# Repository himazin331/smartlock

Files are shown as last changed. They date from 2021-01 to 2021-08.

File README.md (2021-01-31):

# セキュアなスマートロックを作りたい

## 概要
**顔認証**(生体)とスマホの**MACアドレス認証**(所有)の二要素認証で解錠するスマートロックをつくる。
また、遠隔でも解錠/施錠できるようにWebアプリケーションを通じて制御できるようにする。

玄関ドアの外側に**TTGO T-camera**(人感センサー付カメラ)を取り付ける。モバイルバッテリーなどで供給する。(ドアの構造上及びコンセントがないため)

消費電力を抑えるために、施錠状態かつ人を感知したときにのみ認証を試みる。

スマホのMACアドレスは自宅WiFiに自動接続されたときにarpコマンドにより取得する。

## システム構成
システム構成図

 - **Webアプリケーション**
AAA.himazin331.comはCGI用FQDN。BBB.himazin331.comはラズパイ用FQDN(サブドメインは秘匿)
AAA.himazin331.comはSSL/TLS暗号化させMixed Content回避。BBB.himazin331.comはDDNSによって自宅のグローバルIPと紐付ける。

- **認証**
TTGO T-cameraはSTAモードで稼働させ自宅LANに接続させる。
UDP通信では、ラズパイがT-cameraに施錠状態であることを伝える、T-cameraがラズパイに人を感知したことを伝えることをする。
HTTP通信ではラズパイがT-cameraのカメラサーバーにリクエストし、カメラ画像を取得する。

BBB.himazin331.comをSSL/TLS暗号化させれば楽なのだが、私のネットワーク環境はIPv6 IPoE(IPv4 over IPv6)のため80, 443番ポートを開放できず、Let's EncryptのHTTP-01チャレンジができなかった。また、ラズパイ - Azure間をOpenVPNで通信の秘匿化を図ったが、なぜかWebページが表示されなくなってしまったので断念。

## シーケンス図

### Webアプリケーション
Webアプリケーション-シーケンス図

### 認証
認証 - シーケンス図

## 回路図
回路図

入力コンデンサ0.033μFとあるが、0.33μFが適切である。([datasheet](https://akizukidenshi.com/download/ds/st/l78.pdf)より)
しかし、手違いで0.033μFのコンデンサ使い実装してしまった。
一応、動作に影響はないが差し替える予定。

## 実体配線図
実体配線図

当初はGPIO 4番を使う予定だったが、実装中に短絡して不能になってしまったため、GPIO 14番に変更。

## 使用ハードウェア
- Azure VM (米国西部2 CentOS 7.8.2003 Standard B1s (1 vcpu 数、1 GiB メモリ))
- Raspberry Pi Zero WH
- MG996R ([datasheet](https://akizukidenshi.com/download/ds/towerpro/mg996r.pdf))
- 9V-2A ACアダプタ
- 三端子レギュレータ L7806CV ([datasheet](https://akizukidenshi.com/download/ds/st/l78.pdf))
- MOS-FET INK021ABS1-T112 ([datasheet](https://akizukidenshi.com/download/ds/isahaya/INK021ABS1_J.pdf))
- その他電子部品
- TTGO T-Camera ESP32 WROVER & PSRAM Camera Module ([商品リンク](https://www.amazon.co.jp/gp/product/B07PPR8Z2S/))
- 適当なモバイルバッテリー
- 3Dプリンタ (ガワ造形)

## 使用言語
- Python
- C/C++
- HTML/CSS
- Javascript

## 使用ライブラリ
- Apache
- Ajax
- Tensorflow, Tensorflow Lite
- pigpio
- OpenCV
- [T-camera Demo Program](https://github.com/lewisxhe/esp32-camera-series
)

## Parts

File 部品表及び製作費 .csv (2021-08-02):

名称 | 数量 | 購入場所 | 価格(税込) | 備考
ANYCUBIC PLA樹脂 1.75mm フィラメント シルバー | 146 g | Amazon | ¥423 | 1kg ¥2,899 サムターンマウンタ: 20g サーボモータ固定マウンタ: 44g 制御基板ステージ: 31g 制御基板ステージ蓋: 13g T-cameraマウント: 14g ケーブルフック: 6g x 4
Raspberry Pi Zero WH | 1 | Raspberry Pi Shop by KSY | ¥1,848 | 送料 ¥550
MG996R | 1 | Amazon | ¥1,450 | 送料 ¥200 データシート: https://akizukidenshi.com/download/ds/towerpro/mg996r.pdf
TTGO T-Camera ESP32 WROVER & PSRAM Camera Module | 1 | Amazon | ¥2,300
三端子レギュレーター Ｌ７８０６ＣＶ | 1 | 秋月電子 | ¥25 | 出力 ６Ｖ１．５Ａ データシート: https://akizukidenshi.com/download/ds/st/l78.pdf
Nch MOS-FET INK021ABS1-T112 | 1 | 秋月電子 | ¥70 | VDSS=100V ID=1.4A Vth=1.0~2.5V RDS=200mΩ データシート: https://akizukidenshi.com/download/ds/isahaya/INK021ABS1_J.pdf
ブレッドボード用ＤＣジャックＤＩＰ化キット | 1 | 秋月電子 | ¥100
小型３Ｐトグルスイッチ | 1 | 秋月電子 | ¥80
積層セラミックコンデンサー 0.1μF 50V | 1 | いただきもの | ¥0
積層セラミックコンデンサー 0.033μF 50V | 1 | 秋月電子 | ¥10 | 手違いでこちらを使用 動作には影響なし。
５ｍｍ黄緑色ＬＥＤ ５７０ｎｍ ＯＳＮＧ５１１３Ａ | 1 | 秋月電子 | ¥5
抵抗器 10Ω | 1 | その辺に転がってた | ¥0 | 金属皮膜抵抗？
抵抗器 100Ω | 1 | その辺に転がってた | ¥0 | 金属皮膜抵抗？
抵抗器 10kΩ | 1 | その辺に転がってた | ¥0 | 金属皮膜抵抗？
ピンヘッダ | 2 | その辺に転がってた | ¥0
メス-メス ジャンパーワイヤ | 3 | 秋月電子 | ¥99 | 10本入り ¥330
片面ガラスコンポジット・ユニバーサル基板 | 1 | 秋月電子 | ¥60
9V 2A ACアダプタ | 1 | いただきもの | ¥0
DCプラグ付ケーブル | 1 | いただきもの | ¥0
microUSBケーブル | 2 | その辺に転がってた | ¥0
USB ACアダプタ | 1 | その辺に転がってた | ¥0
延長ケーブル | 1 | ホームセンター | ¥712 | 3m
ネジ M3 | 1 | ホームセンター | ¥8
ネジ M2.6 | 4 | その辺に転がってた | ¥0
ネオジム磁石 | 10 | ダイソー | ¥330 | 小: 6個 中: 4個
モバイルバッテリー | 1 | その辺に転がってた | ¥0 | 20000mAh
3M コマンドタブ | 1 | ホームセンター | ¥17
合計 | ¥7,537

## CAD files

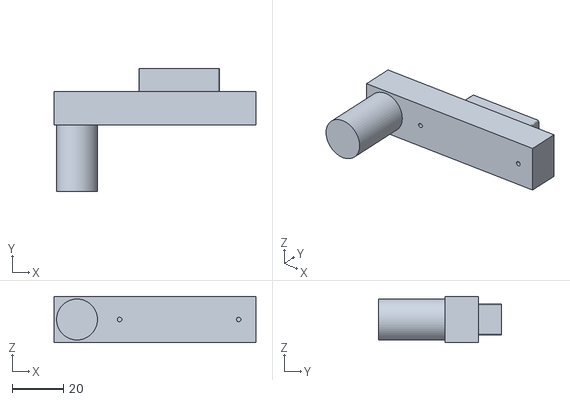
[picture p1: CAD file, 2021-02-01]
3Dprint/key_mounter.stl
79.0 x 48.0 x 18.0

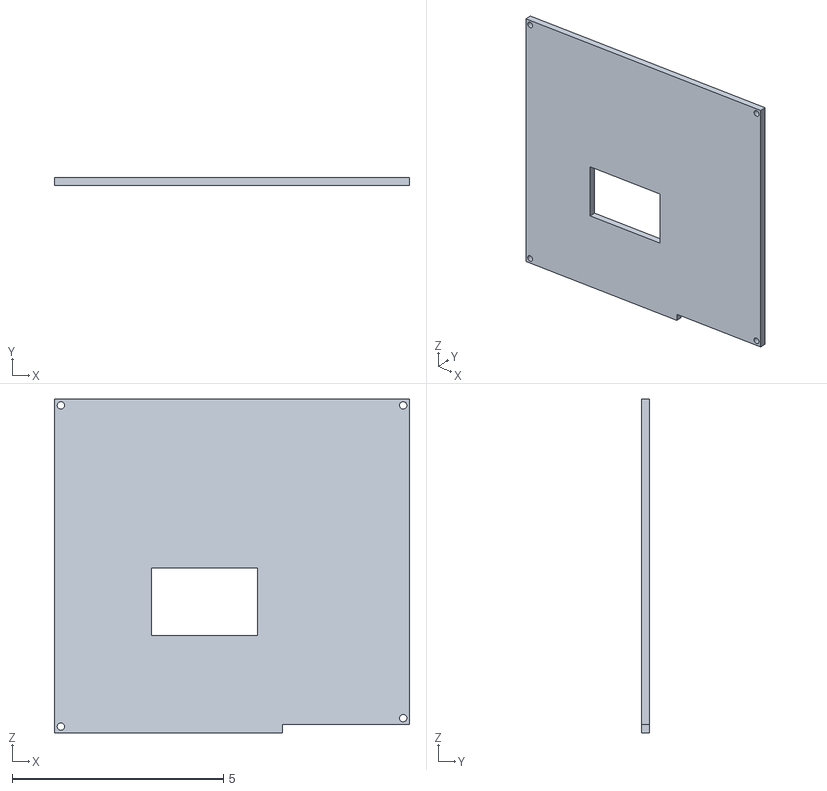
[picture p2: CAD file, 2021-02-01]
3Dprint/kiban_stage_huta.stl
8.40 x 0.2 x 7.90

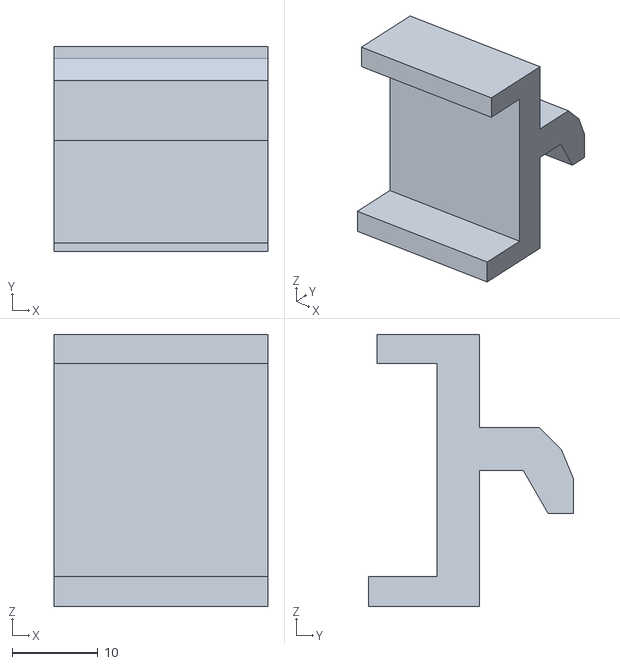
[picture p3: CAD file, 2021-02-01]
3Dprint/cable_hook.stl
25.0 x 24.0 x 31.8

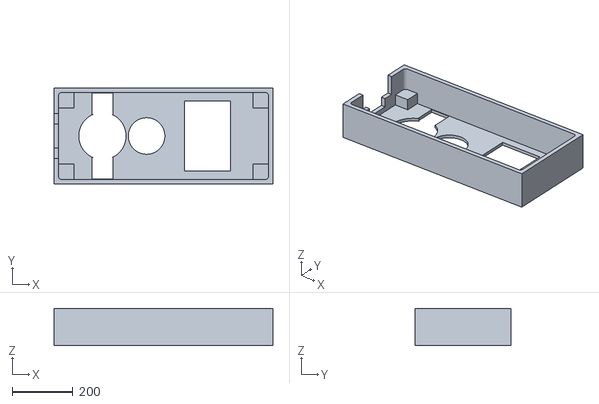
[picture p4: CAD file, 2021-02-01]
3Dprint/t-camera_huta.stl
719.0 x 315.0 x 122.0

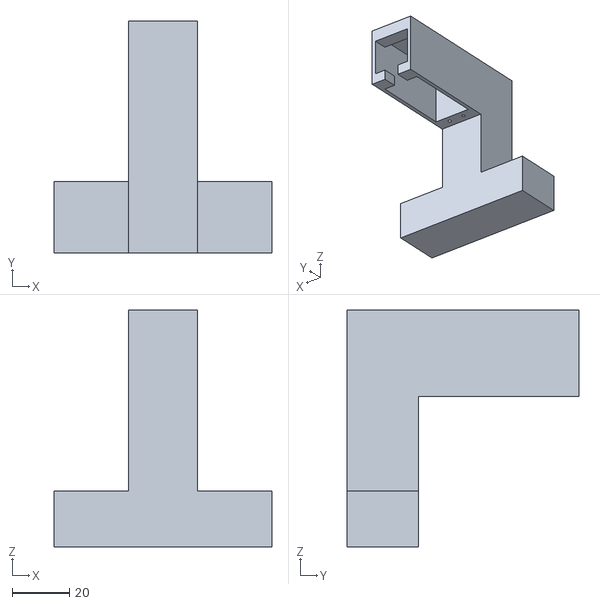
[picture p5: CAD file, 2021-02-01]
3Dprint/motor_mount.stl
76.0 x 81.0 x 82.8

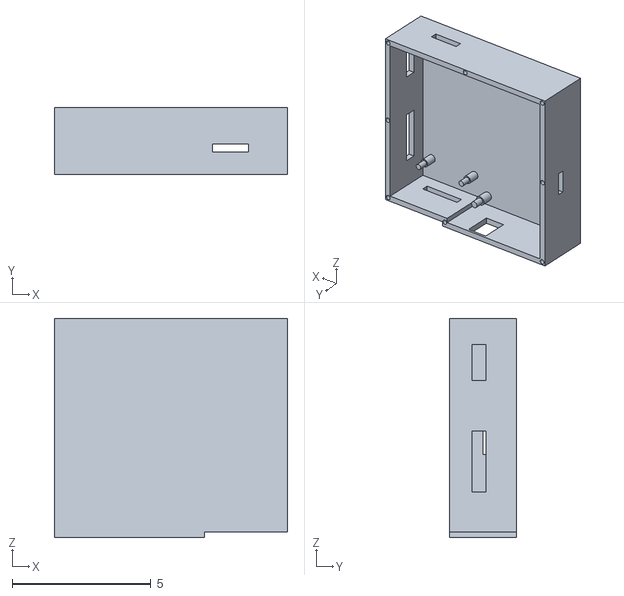
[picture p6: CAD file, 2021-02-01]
3Dprint/kiban_stage.stl
8.40 x 2.40 x 7.90

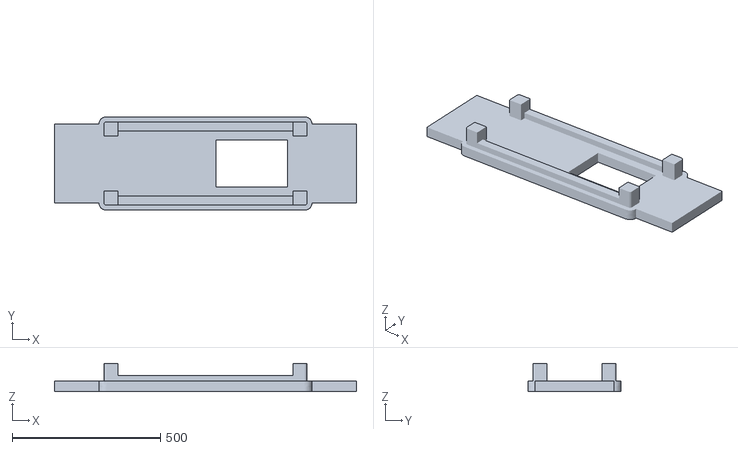
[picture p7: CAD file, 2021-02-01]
3Dprint/t-camera_stage.stl
1019.0 x 315.0 x 95.0

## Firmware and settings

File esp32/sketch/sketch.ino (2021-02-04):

#include <WiFi.h> // WiFi関連のヘッダーファイル
#include <WiFiUdp.h>  // UDP関連のヘッダーファイル
#include <Wire.h> // I2C関連のヘッダーファイル
#include <string.h>
#include "esp_camera.h" // カメラ関連のヘッダーファイル

#include "select_pins.h" // センサーやカメラなどのピン情報

// アクセスポイントモード
// #define SOFTAP_MODE
#if defined(SOFTAP_MODE)
#endif

// 自動スリープ時使用 (今回は不要)
#define uS_TO_S_FACTOR 1000000 // μS -> S変換
#define TIME_TO_SLEEP  5 // 自動スリープになる時間(秒)

// 無線LAN情報
#define WIFI_SSID   "rs500m-6ae9a6-1"
#define WIFI_PASSWD "7b8b88151fc22"
String macAddress = ""; // MACアドレス
String ipAddress = "";  // IPアドレス

// Raspberry Pi情報
static WiFiUDP udp;
static const char *raspip = "192.168.1.8";
static const int raspport = 6100;

char udp_data[128]; // UDP受信データ

extern void startCameraServer();

// ボタン アクティブ
#include <OneButton.h>
OneButton button(BUTTON_1, true);

// ディスプレイ アクティブ
#include "SSD1306.h"
#include "OLEDDisplayUi.h"
#define SSD1306_ADDRESS 0x3c
SSD1306 oled(SSD1306_ADDRESS, I2C_SDA, I2C_SCL, (OLEDDISPLAY_GEOMETRY)SSD130_MODLE_TYPE);
OLEDDisplayUi ui(&oled);

bool deviceProbe(uint8_t addr)
{
  Wire.beginTransmission(addr);
  return Wire.endTransmission() == 0;
}

// ディスプレイ セットアップ
bool setupDisplay()
{
  // セットアップ失敗 -> 中断
  if (!deviceProbe(SSD1306_ADDRESS))return false;
  
  oled.init();
  oled.setTextAlignment(TEXT_ALIGN_CENTER); // 中央揃え
  oled.setFont(ArialMT_Plain_16);           // フォント

  // 起動画面 表示
  oled.drawString(oled.getWidth() / 2, oled.getHeight() / 2 - 16, "SmartLock");
  oled.drawString(oled.getWidth() / 2, oled.getHeight() / 2, "System");
  oled.display();

  return true;
}

// ディスプレイ出力
void smartlock()
{
  // PIR反応 -> 認証開始
  while (digitalRead(AS312_PIN))
  {
    // ボタン反応 有効
    button.tick();

    // PIR反応フラグをRaspに送信
    udp.beginPacket(raspip, raspport);
    udp.write('1');
    udp.endPacket();
    delay(500);
    
    oled.clear();

    oled.setTextAlignment(TEXT_ALIGN_CENTER); // 中央揃え
    oled.setFont(ArialMT_Plain_16); // フォント

    Serial.println("Authentication...");
    oled.drawString(oled.getWidth() / 2, oled.getHeight() / 2 - 16, "Authentication");
    oled.display();
  }

  oled.clear(); // 画面初期化

  oled.setTextAlignment(TEXT_ALIGN_CENTER); // 中央揃え
  oled.setFont(ArialMT_Plain_16); // フォント

  oled.drawString(oled.getWidth() / 2, oled.getHeight() / 2 - 16, "SmartLock");
  oled.drawString(oled.getWidth() / 2, oled.getHeight() / 2, "System");
  oled.display();
}

// 外部電源供給 セットアップ
bool setupPower()
{
  #define IP5306_ADDR 0X75
  #define IP5306_REG_SYS_CTL0 0x00
  
  // セットアップ失敗 -> 中断
  if (!deviceProbe(IP5306_ADDR))return false;
  
  // セットアップ
  bool en = true;
  Wire.beginTransmission(IP5306_ADDR);
  Wire.write(IP5306_REG_SYS_CTL0);
  if (en)
    Wire.write(0x37);
  else
    Wire.write(0x35);
  return Wire.endTransmission() == 0;

  return true;
}

// 人感センサー セットアップ
bool setupSensor()
{
  pinMode(AS312_PIN, INPUT);
  return true;
}

// カメラ セットアップ
bool setupCamera()
{
  camera_config_t config;

  #if defined(Y2_GPIO_NUM)
    config.ledc_channel = LEDC_CHANNEL_0;
    config.ledc_timer = LEDC_TIMER_0;
    config.pin_d0 = Y2_GPIO_NUM;
    config.pin_d1 = Y3_GPIO_NUM;
    config.pin_d2 = Y4_GPIO_NUM;
    config.pin_d3 = Y5_GPIO_NUM;
    config.pin_d4 = Y6_GPIO_NUM;
    config.pin_d5 = Y7_GPIO_NUM;
    config.pin_d6 = Y8_GPIO_NUM;
    config.pin_d7 = Y9_GPIO_NUM;
    config.pin_xclk = XCLK_GPIO_NUM;
    config.pin_pclk = PCLK_GPIO_NUM;
    config.pin_vsync = VSYNC_GPIO_NUM;
    config.pin_href = HREF_GPIO_NUM;
    config.pin_sscb_sda = SIOD_GPIO_NUM;
    config.pin_sscb_scl = SIOC_GPIO_NUM;
    config.pin_pwdn = PWDN_GPIO_NUM;
    config.pin_reset = RESET_GPIO_NUM;
    config.xclk_freq_hz = 20000000;
    config.pixel_format = PIXFORMAT_JPEG;
    //init with high specs to pre-allocate larger buffers
    if (psramFound()) {
      config.frame_size = FRAMESIZE_UXGA;
      config.jpeg_quality = 10;
      config.fb_count = 2;
    } else {
      config.frame_size = FRAMESIZE_SVGA;
      config.jpeg_quality = 12;
      config.fb_count = 1;
    }
  #endif

  // セットアップ失敗 -> 中断
  esp_err_t err = esp_camera_init(&config);
  if (err != ESP_OK) {
    Serial.printf("Camera init failed with error 0x%x\n", err);
    return false;
  }

  sensor_t *s = esp_camera_sensor_get();
  // 反転
  s->set_hmirror(s, 1);
  s->set_vflip(s, 1);

  return true;
}

// ボタン セットアップ
void setupButton()
{
  // 2回プッシュ -> スリープモード
  button.attachDoubleClick([]() {    
    ui.disableAutoTransition(); // スライドアニメーション無効

    oled.setTextAlignment(TEXT_ALIGN_CENTER); // 中央揃え
    oled.setFont(ArialMT_Plain_10); // フォント
    oled.clear(); // 画面初期化

    // スリープモード移行表示
    Serial.println("Sleep mode");
    oled.drawString(oled.getWidth() / 2 - 5, oled.getHeight() / 2 - 20, "Transition to sleep mode...");
    oled.drawString(oled.getWidth() / 2, oled.getHeight() / 2, "Press the button");
    oled.drawString(oled.getWidth() / 2, oled.getHeight() / 2 + 10, "to wake up.");
    oled.display();
    delay(3000);

    // ディスプレイ出力OFF
    oled.clear();
    oled.displayOff();

    // スリープモード移行
    esp_sleep_enable_ext1_wakeup(((uint64_t)(((uint64_t)1) << BUTTON_1)), ESP_EXT1_WAKEUP_ALL_LOW); // 復帰条件
    esp_deep_sleep_start();
  });
}

// ネットワーク セットアップ
void setupNetwork()
{
  macAddress = "LilyGo-CAM-";

  // アクセスポイントモード
  #ifdef SOFTAP_MODE
    WiFi.mode(WIFI_AP);
    macAddress += WiFi.softAPmacAddress().substring(0, 5);
    WiFi.softAP(macAddress.c_str());
    ipAddress = WiFi.softAPIP().toString();
  #else // ステーションモード
    WiFi.begin(WIFI_SSID, WIFI_PASSWD);
    while (WiFi.status() != WL_CONNECTED) {
      delay(500);
      Serial.print(".");
    }
    Serial.println("");
    Serial.println("WiFi connected");
    ipAddress = WiFi.localIP().toString();
    macAddress += WiFi.macAddress().substring(0, 5);
  #endif
}

// UDP セットアップ
void setupUDP()
{
  udp.begin(6000);
}

// セットアップ
void setup()
{
  // シリアル通信開始 (115200bps)
  Serial.begin(115200);
  Wire.begin(I2C_SDA, I2C_SCL);

  bool status;
  // ディスプレイ セットアップ
  status = setupDisplay();
  Serial.print("setupDisplay status: "); Serial.println(status);

  // 外部電源供給 セットアップ
  status = setupPower();
  Serial.print("setupPower status: "); Serial.println(status);

  // 人感センサー セットアップ
  status = setupSensor();
  Serial.print("setupSensor status: "); Serial.println(status);

  // カメラ セットアップ
  status = setupCamera();
  Serial.print("setupCamera status: "); Serial.println(status);

  // セットアップ失敗 -> 再試行
  if (!status) {
    delay(10000);
    esp_restart();
  }

  // ボタン セットアップ
  setupButton();
  // ネットワーク セットアップ
  setupNetwork();
  // UDP セットアップ
  setupUDP();
  // Start
  startCameraServer();

  // IPアドレス情報 シリアルモニター出力
  Serial.print("IP Address: "); Serial.println(ipAddress);
}

// ディスプレイ出力
void loop()
{
  // 施錠フラグ Trueならば
  if (udp.parsePacket()) {
    udp.read(udp_data, 128);
    if (strcmp(udp_data, "lock") == 0)
    {
      smartlock();
    }
  }
}

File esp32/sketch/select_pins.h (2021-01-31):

#define PWDN_GPIO_NUM       -1
#define RESET_GPIO_NUM      -1
#define XCLK_GPIO_NUM       32
#define SIOD_GPIO_NUM       13
#define SIOC_GPIO_NUM       12

#define Y9_GPIO_NUM         39
#define Y8_GPIO_NUM         36
#define Y7_GPIO_NUM         23
#define Y6_GPIO_NUM         18
#define Y5_GPIO_NUM         15
#define Y4_GPIO_NUM         4
#define Y3_GPIO_NUM         14
#define Y2_GPIO_NUM         5

#define VSYNC_GPIO_NUM      27
#define HREF_GPIO_NUM       25
#define PCLK_GPIO_NUM       19

#define I2C_SDA             21
#define I2C_SCL             22

#define BUTTON_1            34

#define SSD130_MODLE_TYPE   0

#define AS312_PIN           33

#define ENABLE_IP5306

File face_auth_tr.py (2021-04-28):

import os
import numpy as np

import tensorflow as tf
import tensorflow.keras.layers as kl

import matplotlib.pyplot as plt

os.environ['TF_CPP_MIN_LOG_LEVEL'] = '2'  # TFメッセージ非表示


class Trainer():
    def __init__(self, img_size=96):
        # 画像サイズ
        img_shape = (img_size, img_size, 3)

        # MobileNetV2
        base_model = tf.keras.applications.MobileNetV2(input_shape=img_shape,
                                                        include_top=False, weights='imagenet')
        base_model.trainable = False
        global_average_layer = kl.GlobalAveragePooling2D()
        prediction_layer = kl.Dense(2)

        # 訓練モデル
        self.model = tf.keras.Sequential([
            base_model,
            global_average_layer,
            prediction_layer
        ])

        self.model.compile(optimizer=tf.keras.optimizers.Adam(),
                            loss=tf.keras.losses.BinaryCrossentropy(),
                            metrics=['accuracy'])

    # 訓練
    def train(self, dataset, batch_size, epoch, out_dir):
        train_img, train_lab = dataset

        his = self.model.fit(train_img, train_lab, batch_size=batch_size, epochs=epoch)

        # tflite形式で保存
        converter = tf.lite.TFLiteConverter.from_keras_model(self.model)
        tflite_model = converter.convert()
        open("./converted_model.tflite", "wb").write(tflite_model)

        return his


# データセット作成
def create_dataset(data_dir, channel):
    print("\n___Creating a dataset...")

    cnt = 0
    cnt_t = 0
    prc = ['/', '-', '\\', '|']

    # 画像データの個数
    for c in os.listdir(data_dir):
        d = os.path.join(data_dir, c)
        print("Number of image in a directory \"{}\": {}".format(c, len(os.listdir(d))))

    train_img = []  # 画像データ(テンソル)
    train_lab = []  # ラベル
    label = 0

    for c in os.listdir(data_dir):
        print("\nclass: {},   class id: {}".format(c, label))   # 画像フォルダ名とクラスIDの出力

        d = os.path.join(data_dir, c)                # フォルダ名と画像フォルダ名の結合
        imgs = os.listdir(d)

        # JPEG形式の画像データだけを読込
        for i in [f for f in imgs if ('jpg' or 'JPG' in f)]:
            # キャッシュファイルをスルー
            if i == 'Thumbs.db':
                continue

            img = tf.io.read_file(os.path.join(d, i))       # 画像フォルダパスと画像パスを結合後、読込
            img = tf.image.decode_image(img, channels=channel)    # Tensorflowフォーマットに従ってデコード
            img /= 255     # 正規化

            train_img.append(img)       # 画像データ(テンソル)追加
            train_lab.append(label)     # ラベル追加

            cnt += 1
            cnt_t += 1
            print("\r   Loading a images and labels...{}    ({} / {})".format(prc[cnt_t % 4], cnt, len(os.listdir(d))), end='')
        print("\r   Loading a images and labels...Done    ({} / {})".format(cnt, len(os.listdir(d))), end='')

        label += 1
        cnt = 0
    train_img = tf.convert_to_tensor(train_img, np.float32)  # 画像データセット
    train_lab = tf.convert_to_tensor(train_lab, np.int64)    # ラベルデータセット
    print("\n___Successfully completed\n")

    return train_img, train_lab


def graph_output(history):
    # 予測精度グラフ
    plt.plot(history.history['accuracy'])
    plt.title('Model accuracy')
    plt.ylabel('Accuracy')
    plt.xlabel('Epoch')
    plt.legend(['Train'], loc='upper left')
    plt.show()

    # 損失値グラフ
    plt.plot(history.history['loss'])
    plt.title('Model loss')
    plt.ylabel('Loss')
    plt.xlabel('Epoch')
    plt.legend(['Train'], loc='upper left')
    plt.show()


def main():
    # 訓練データフォルダ
    train_dir = os.path.abspath("train_data")
    # 保存先フォルダ
    out_dir = os.path.join(os.path.dirname(os.path.abspath(__file__)), "result")
    os.makedirs(out_dir, exist_ok=True)  # フォルダ作成
    img_size = 96       # 画像サイズ(N x N)
    channel = 3         # 出力チャンネル数
    batch_size = 32     # ミニバッチサイズ
    epoch = 8           # 訓練回数

    # 設定情報出力
    print("=== Setting information ===")
    print("# Output directory: {}".format(out_dir))
    print("# Train directory: {}".format(train_dir))
    print("# Images size: {}".format(img_size))
    print("# Channel: {}".format(channel))
    print("# Minibatch-size: {}".format(batch_size))
    print("# Epoch: {}".format(epoch))
    print("===========================\n")

    # データセット作成
    dataset = create_dataset(train_dir, channel)

    # 学習
    trainer = Trainer(img_size)
    his = trainer.train(dataset, batch_size, epoch, out_dir)

    # 精度, 損失値グラフ出力
    graph_output(his)


if __name__ == '__main__':
    main()

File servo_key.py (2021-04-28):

import pigpio
import time
import datetime
import pytz
import csv
import os


class key():
    def __init__(self):
        self.swpin = 3  # MOS-FET制御信号ピン
        self.pin = 14   # パルス信号ピン
        self.pi = pigpio.pi()

    # 施錠
    def lock(self):
        # 手動操作閉鎖
        self.pi.write(self.swpin, 1)
        time.sleep(0.5)
        # 駆動
        self.pi.set_servo_pulsewidth(self.pin, 1445)
        # 手動操作開放
        self.pi.write(self.swpin, 0)
        time.sleep(0.5)

        self.writelog("Lock")  # ログ書き込み

    # 解錠
    def unlock(self):
        # 手動操作閉鎖
        self.pi.write(self.swpin, 1)
        time.sleep(0.5)
        # 駆動
        self.pi.set_servo_pulsewidth(self.pin, 520)
        # 手動操作開放
        self.pi.write(self.swpin, 0)
        time.sleep(0.5)

        self.writelog("Unlock")  # ログ書き込み

    # ログ書き込み
    def writelog(self, str):
        with open('/var/www/html/log/log.csv', 'a') as f:
            now = datetime.datetime.now(pytz.timezone('Asia/Tokyo'))
            writer = csv.writer(f)
            writer.writerow([now.strftime("%Y/%m/%d %H:%M:%S"), str])
    
    # ログ読み込み
    def readlog(self):
        # ログ未存在なら作成
        if not os.path.exists('/var/www/html/log/log.csv'):
            with open('/var/www/html/log/log.csv', 'w') as f:
                os.chmod('/var/www/html/log/log.csv', 0o777)  # フルコントロール権限

                writer = csv.writer(f)
                writer.writerow(['----/--/-- --:--:--', "Lock"])

        r = {}
        # ログ読み込み
        with open('/var/www/html/log/log.csv', 'r') as f:
            reader = csv.reader(f)
            logs = [row[0] + "\t" + row[1] for row in reader]

        # 現在のステータス取得
        if "Lock" in logs[-1]:
            r['status'] = 1
        elif "Unlock" in logs[-1]:
            r['status'] = 0

        logs.reverse()
        r['log'] = logs

        # ログ行数が11行以上なら削除
        if len(logs) > 10:
            os.remove('/var/www/html/log/log.csv')  # 消去
            # 直近のログ１つのみ書き込み
            with open('/var/www/html/log/log.csv', 'w') as f:
                os.chmod('/var/www/html/log/log.csv', 0o777)  # フルコントロール権限

                writer = csv.writer(f)
                writer.writerow(logs[0].split('\t'))

        return r

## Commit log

2021-01-31 Servo Motor Control
2021-01-31 T-camera ESP32 program
2021-02-01 3D Model STL
    [cable_hook.stl, key_mounter.stl, kiban_stage.stl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]
2021-02-02 Get Camera Image
2021-08-02 部品表及び制作費
    [部品表及び製作費.xlsx]
2021-08-02 部品表及び製作費
    [部品表及び製作費 .csv]
